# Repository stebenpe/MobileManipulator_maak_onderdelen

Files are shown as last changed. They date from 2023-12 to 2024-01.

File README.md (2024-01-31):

# Maak onderdelen
Om de robot arm op de AMR te plaatsen is een tussen frame nodig. Hier zal ook meteen alle besturingsonderdelen van de MoMa in worden geplaatst. Het frame bestaat uit 4040 en 2020 aluminium frames met beplating er omheen voor stevigheid en afscherming. In het frame zit de besturingskast van de robot arm, safety PLC, embedded AI computer, router en bedingingspaneel met noodstop. De beplating is watergesneden, gebogen, getapped en verzonken. verder zijn er een aantal onderdelen 3D geprint, dit zijn: trap sensoren, houder embedded AI computer, besturingspaneel houder en de kabel buis houders. Dit is geprint met een FDM printer op de trap sensoren na. Deze zijn met een resin printer gemaakt.

## 1. Benodigde onderdelen
1. 2020 ISB aluminium profiel 450mm lang 2X (met M6 getapped gat aan beide kanten)
2. 4040 ISB aluminium profiel 450mm lang 5X
3. ISB M6 t-sleuf 8 moer 20X
4. ISB M5 t-sleuf 5 moer 10X
5. M5X12 verzonken inbus bout 10X
6. M5X20 verzonken inbus bout 4X
7. M5X40 verzonken inbus bout 6X
8. M6X12 verzonken inbus bout 20X
9. 5mm aluminium plaat (voor watersnijden)
10. 3mm aluminium plaat (voor watersnijden)
11. 2mm aluminium plaat (voor watersnijden)
12. M3 inserts 16X (voor de kabel buis 3D print)
13. M6 schroefdraad 500mm lang 5X
14. M6 dopmoer met veer ring en ring 5X
15. M6 moer met ring 1X
16. M10X35 bout met veer ring 2 ringen en een moer 4X

## 2. SolidWorks
Alle onderdelen zijn gemaakt in SolidWorks. Hierin is ook een totaal assembly gemaakt van de MoMa. Hieronder is een renders daarvan te zien.

moma

## 3. 3D prints
De 3D prints zijn gemaakt door een bambu lab en anycubic printer maar een andere 3D printer zou ook moeten werken. De trap sensoren zijn gemaakt door de anycubic 3D printer. Dit is een resin printer, hier is voor gekozen omdat het een best complex onderdeel is met een clip systeem en overhangs. Een resin printer kan dit beter printen dan een FDM printer. De rest van de onderdelen zijn wel geprint door een FDM printer. Dit omdat dit sneller is en minder moeite kost met schoonmaken.

### 3.1 FDM printer
Op de FDM printer zijn de volgende 3D prints genaakt: (als ergens 2X voor staat moet deze 2 keer worden geprint en bij 4X 4 keer)
1. 2X kabel beugel 1.stl
2. 2X kabel beugel 2.stl
3. 2X kabel beugel groot1.stl
4. 2X kabel beugel groot2.stl
5. 4X kabel beugel 3.stl
6. 4X tussen blok controller en top plate.stl
7. 3D print jetson holder boven.stl
8. 3D print jetson holder onder.stl
9. LD 90 panel 3d print.stl

### 3.2 Resin printer
Op de resin printer zijn de volgende 3D prints genaakt:
1. sensor blok L V1.2.stl
2. sensor blok M V1.2.stl
3. sensor blok R V1.2.stl

## 4. Watersnijden
De volgende onderdelen zijn water gesneden: ( als er 2X in staat moet deze 2 keer worden watergesneden. het aan mm van het materiaal zit ook in de naam)
1. 2X side laser holder 2mm.DXF
2. 2X zei plaat 2mm.DXF
3. 3d camera holder 2mm.DXF
4. achterplaat elektra 2mm.DXF
5. Flat pattern - achter plaat sheet metal 2mm.DXF
6. Flat pattern - voor plaat sheet metal 2mm.DXF
7. top plate ld90 3mm.DXF
8. top top plate ld90 5mm.DXF
9. tussen plaat 2X 3mm.DXF
10. tussen plaat met ronding 2X 3mm.DXF

Dit is gedaan met de OMAX 2652 watersnijder:
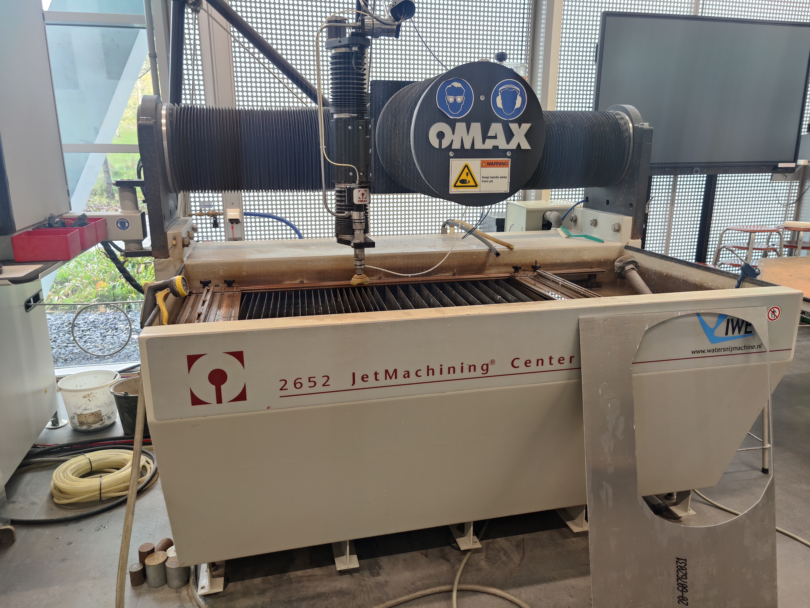
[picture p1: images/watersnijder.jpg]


### 4.1 Buigen
De voor en achter plaat van het frame moeten worden gebogen. Het is handig om eerst een test strip te maken en die te buigen. De voorplaat heeft een lengte nodig van 655,59mm voor de test strip is het handig om deze te af te snijden op een hoogte van 100mm. De achter plaat heeft een lengte van 633,82 en ook hier is het handig om de test strip een hoogte van 100mm te doen. De volgorde van het buigen is eerst de ronding doen en daarna met de kantbank vanaf de buiging naar het einde te werken. De afmetingen en rondingen van de buigen zijn te vinden in de SolidWorks tekening van de betreffende onderdelen. De watergesneden top plate voor de LD-90 is ook goed te gebruiken als referentie bij het buigen. Een voorbeeld van de gebogen test strips is hieronder te zien:



De uiteindelijke platen moeten worden gesneden op een hoogte van 450mm in plaats van de 100mm van de test strips. Ook is het belangrijk om voor het buigen eerst de bramen op de randen weg te halen met vijl en de gaten te verzinken voor een M4 verzonken inbus bout. De test platen kunnen tijdens het buigen ook handig als referentie worden gebruikt.

### 4.2 Verzinken en tappen
De 4 tussenplaten moeten worden getapped met een M4 tap. Verder moeten de voor, achter en zei platen worden verzonken voor een M4 verzonken inbus bout. Let op bij het verzinken dat dit aan de juiste kant wordt gedaan. De voor en achter plaat maakt niet uit maar moet je er vervolgens wel rekening mee houden bij het buigen. Voor de 2 zei platen is het belangrijk dat ze beide aan een andere kant zijn verzonken want deze zijn op die manier gespiegeld. Verder moet er voor de top plate en top top plate verzonken worden voor M6 en M5 verzonken inbus bouten volgens de SolidWorks tekening.

## 5. Trap sensor
Omdat het helaas een keer is gebeurd dat een geleende LD-60 van de trap is gevallen bij NHL-Stenden door de afwezigheid van een trap sensor, hebben we er voor gekozen om een zelfgemaakte trap sensor toe te voegen. Deze zal worden aangesloten op de UserBumper_1-3. Dit werk door een ToF sensor die schuin naar voren kijkt en de data naar een esp32 stuurt. zodra deze een verhoging of verlaging van 30 mm tegen komt zal deze een relais triggeren welke is aangesloten op de UserBumper_1-3 van de LD-90. Hieronder is een programma geschreven in arduino IDE welke te vinden is onder de map trap beveiliging. Hier moet nog een stuk worden toegevoegd voor de WS2812 leds welke in de behuizingen worden geplaatst van de sensoren om de status weer te geven. Hieronder zijn wat renders te zien over hoe het er uit zou moeten zien:

Vooraanzicht 3 trap sensoren             |  Ingezoomd op 1 trap sensor
:-------------------------:|:-------------------------:
  |  

Er is ook een PCB ontworpen voor de trap sensor. De altium bestanden hiervan zijn te vinden in de map trap beveiliging/altium.
Hieronder is een foto te zien van de gemaakte PCB in altium:

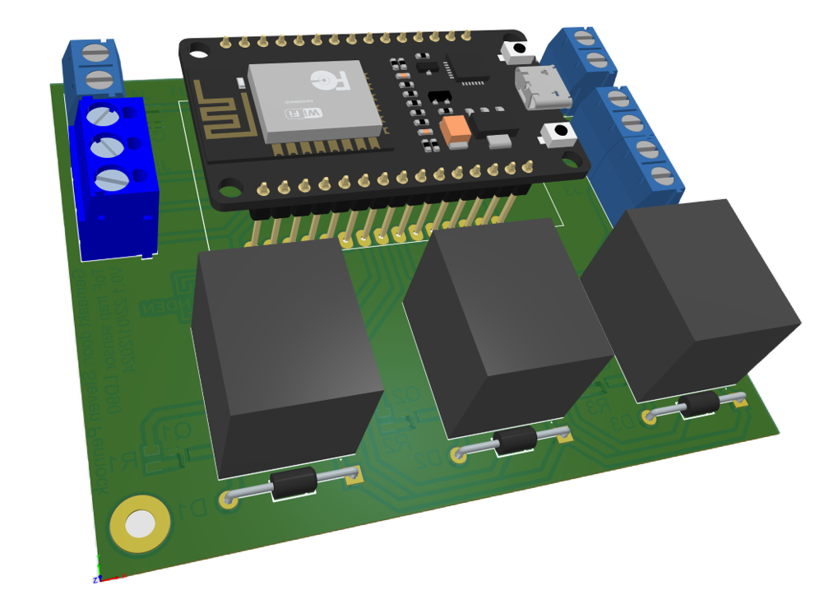
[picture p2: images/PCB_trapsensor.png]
PCB trapsensor


## 6. Monteren en demonteren

### 6.1 Monteren
De montage/demontage van het frame moet met minimaal 2 personen worden gedaan. Dit wegens het gewicht, grote en kostbaarheid.

Bij onduidelijkheden kan je ook kijken naar de SoldWorks assembly, daar is alles te zien zoals de bouten en moeren.

1. Haal de bovenplaat van de LD90 eraf (let op dat er kabels voor de antenne's en HMI aan de LD90 zitten en dat deze niet heel lang zijn).
2. Demonteer de antenne's en de HMI van de bovenplaat. De antenne kabels en de HMI kabel mag bevestigd blijven aan de LD90. De HMI en antenne's moeten wel los worden gehaald van de kabels, deze worden er later weer opgezet.
3. Bevestig de molex connectoren met kabels aan de LD90 IO zoals op onderstaande afbeelding.
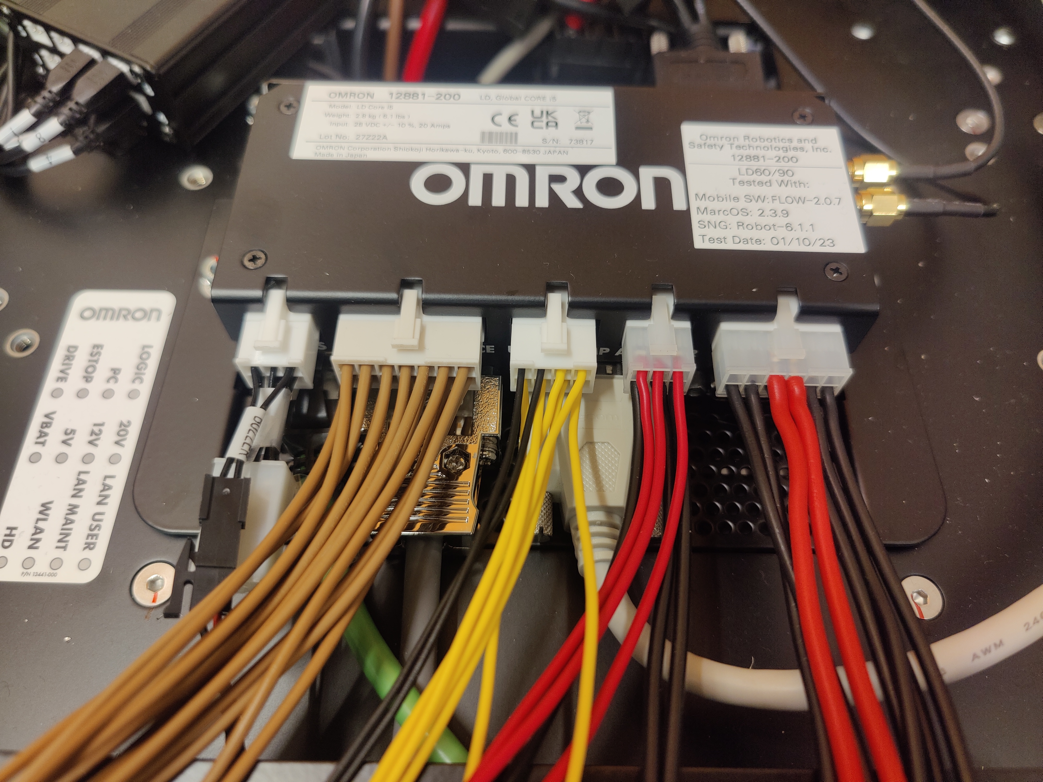
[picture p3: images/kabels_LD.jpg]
kabels


4. Maak de kabels netjes bij elkaar met tie wraps en een spiraalband. Leg alle benodigde kabels bij elkaar aan de voorkant van de LD90, hier zit het gat in de bovenplaat waar de kabels doorheen moeten. Zie onderstaande foto als voorbeeld.
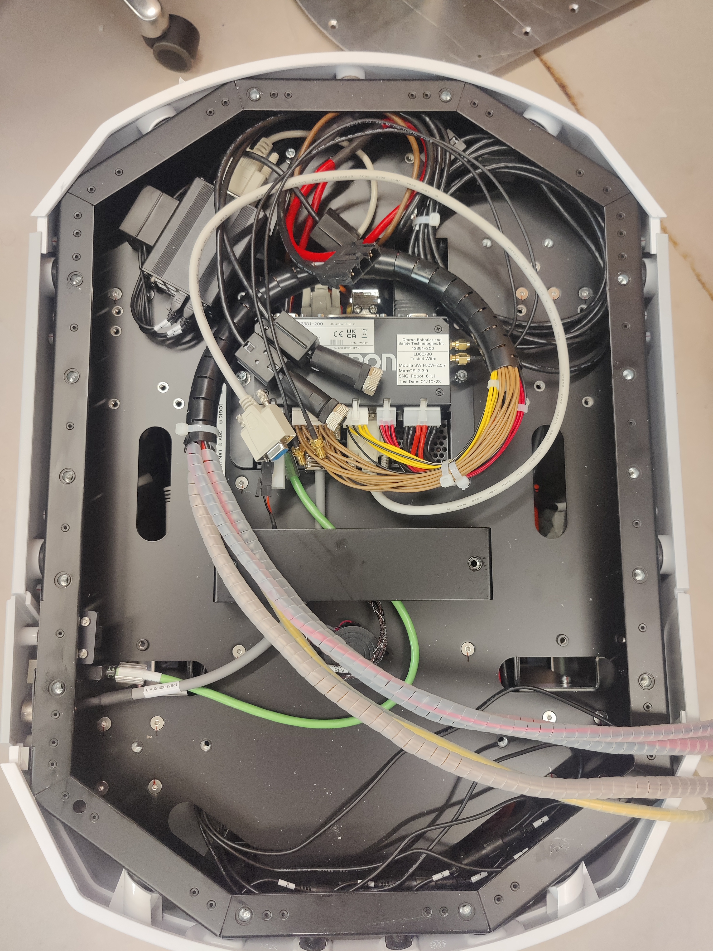
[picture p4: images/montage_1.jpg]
montage_1


5. Vervolgens kan de bovenplaat worden voorbereid voor de montage. Bevestig de robotarm besturingskast en 2020 aluminium frames aan de bovenplaat met M6 verzonken inbus bouten en bevestig 1 van de M6 stafen aan de bovenplaat. De M6 staaf moet wel met een moer en ring aan de onderkant worden bevestigd. Zie onderstaande foto's voor verduidelijking.

Overzicht             |  Moer onder bovenplaat
:-------------------------:|:-------------------------:
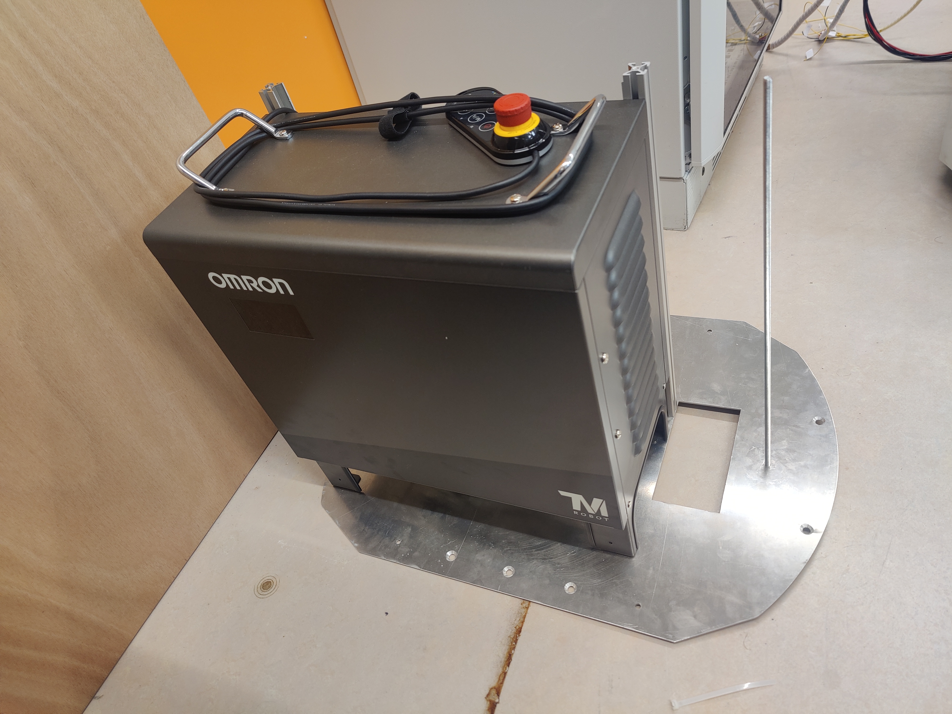
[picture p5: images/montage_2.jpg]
montage_2
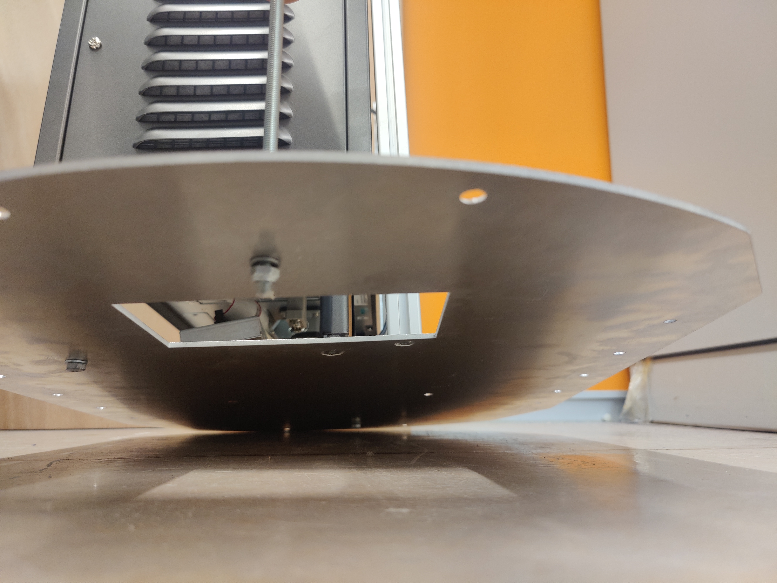
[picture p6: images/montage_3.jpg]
montage_3
  |  

6. Plaats nu de bovenplaat op de LD90. Doe dit met minimaal 2 mensen, 1 iemand die de bovenplaat met besturingskast op de LD90 plaatst en 1 iemand die de kabels door het vierkante gat begeleidt. Dit ziet er dan als volgt uit:
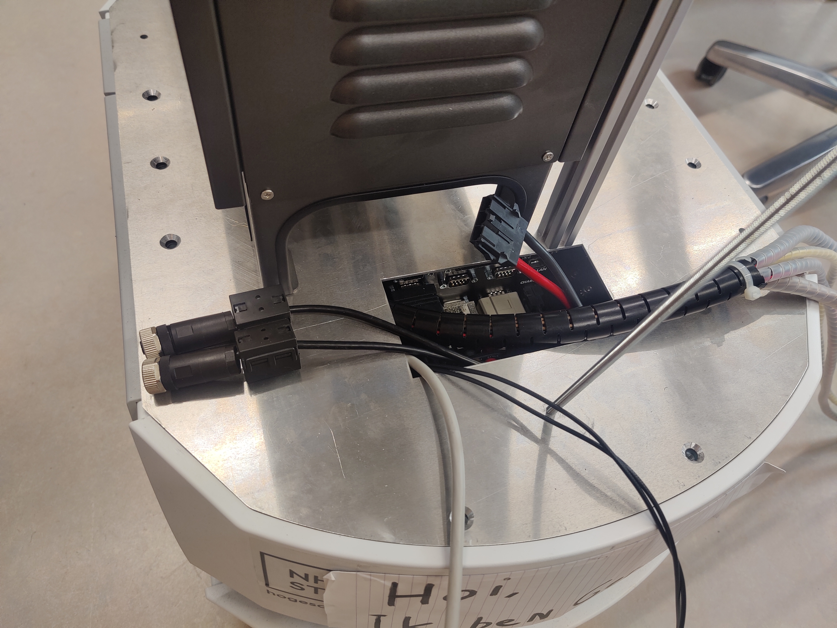
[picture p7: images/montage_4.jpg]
montage_4


7. Bevestig nu een internet kabel aan de user LAN van de LD90. Zie onderstaande foto van de user LAN.
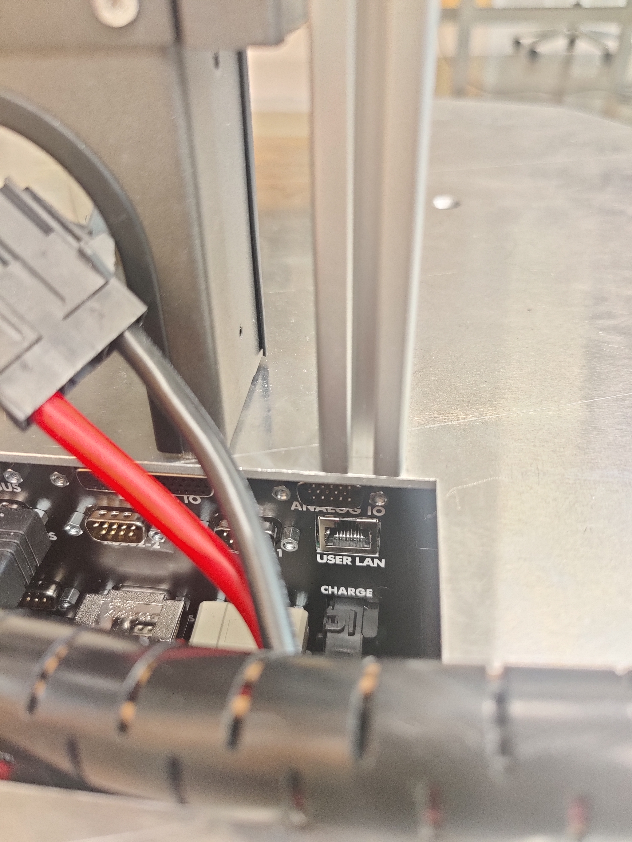
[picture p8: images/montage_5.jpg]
montage_5


8. Plaats de besturingskast op de 2 2020 aluminium profielen en sluit alle kabels aan.

9. Schroef nu de 4 overige M6 stafen aan de bovenplaat. Zie onderstaande foto's voor verduidelijking.
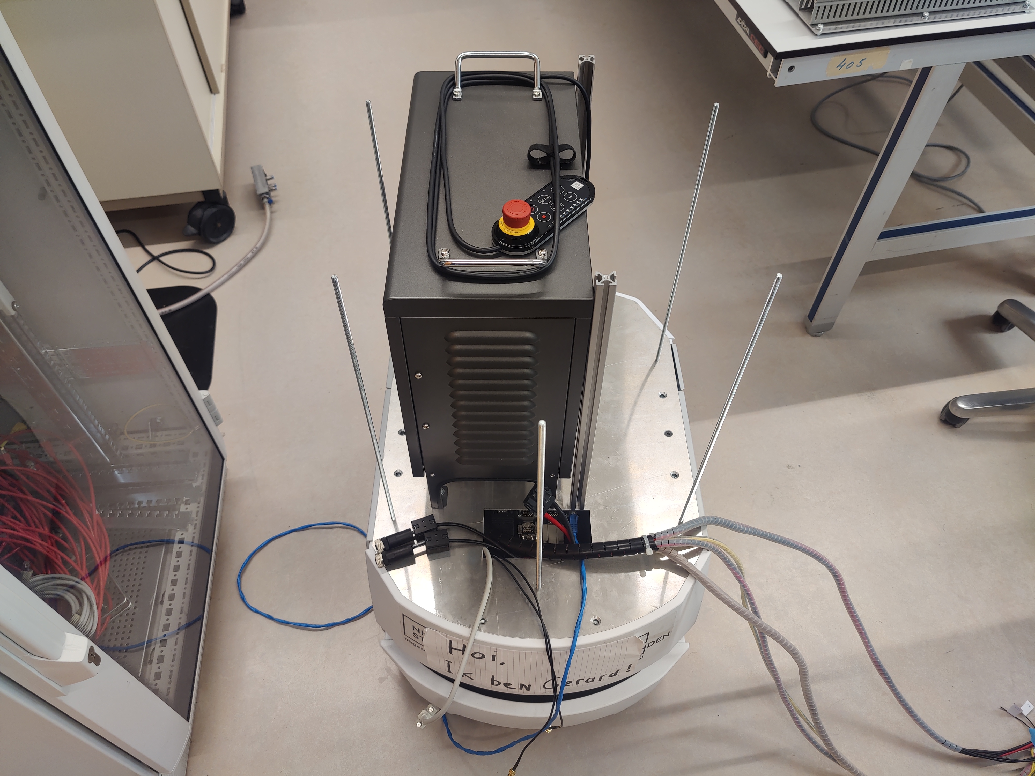
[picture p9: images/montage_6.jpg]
montage_6


10. Bereid de 2 zei platen voor. Hiervoor zijn de volgende onderdelen voor nodig: 4 4040 profielen, 2 zei platen, 2 tussen platen, 2 tussen platen met ronding, 2 side lasers, 2 side laser bevestigingsplaten, 8 M4 verzonken inbus bouten, 6 M6 verzonken inbus bouten en 16 M6 T-sleuf moeren. Zie onderstaande foto van hoe het er uiteindelijk moet uitzien.
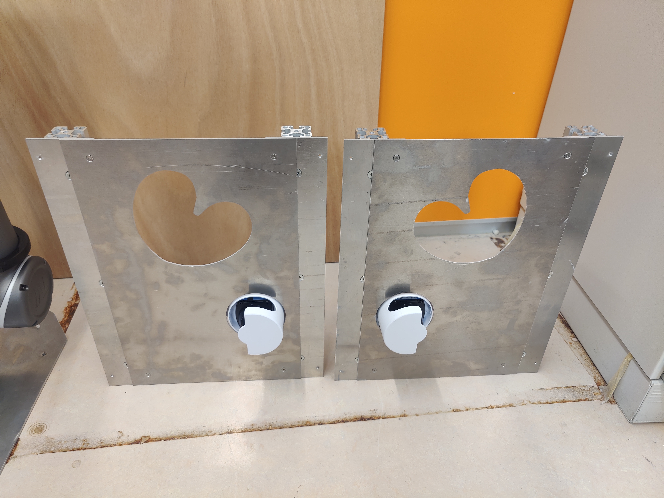
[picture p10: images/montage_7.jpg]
montage_7


11. Plaats de 2 zei platen op de 4 M6 stafen, en plaats de laatste 4040 profiel op de M6 staaf midden voor.

12. Bevestig de HMI en entenne extender kabels op de achterplaat van de LD90. Zie onderstaande foto van de bevestiging van de HMI met de 3D print.

Vooraanzicht             |  Achteraanzicht
:-------------------------:|:-------------------------:
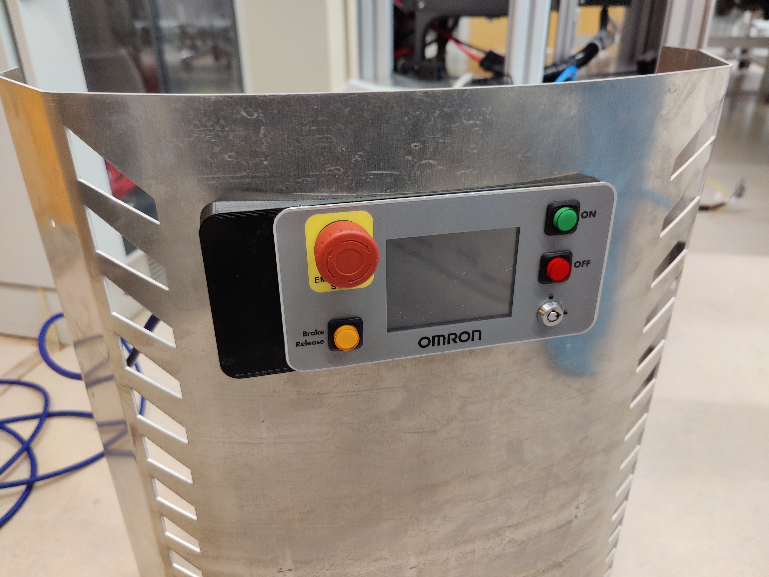
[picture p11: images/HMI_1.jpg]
HMI_1
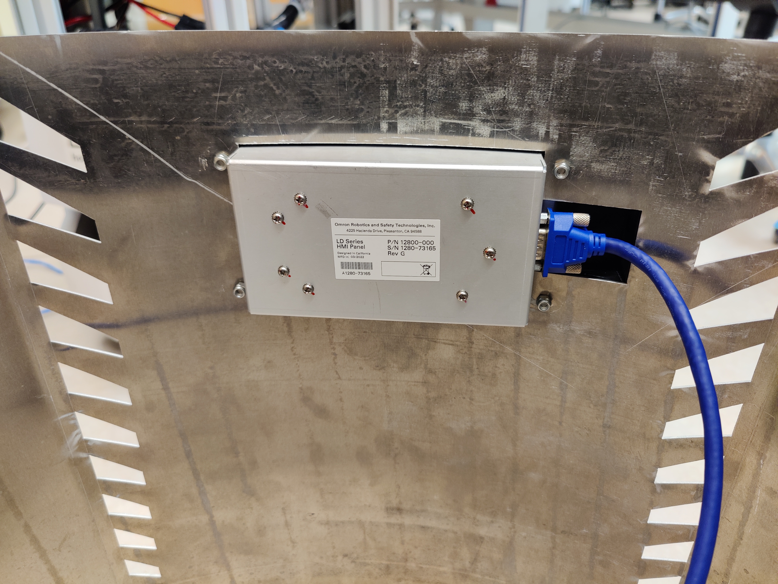
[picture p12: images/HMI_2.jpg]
HMI_2
  |  

## 6.2 Demonteren

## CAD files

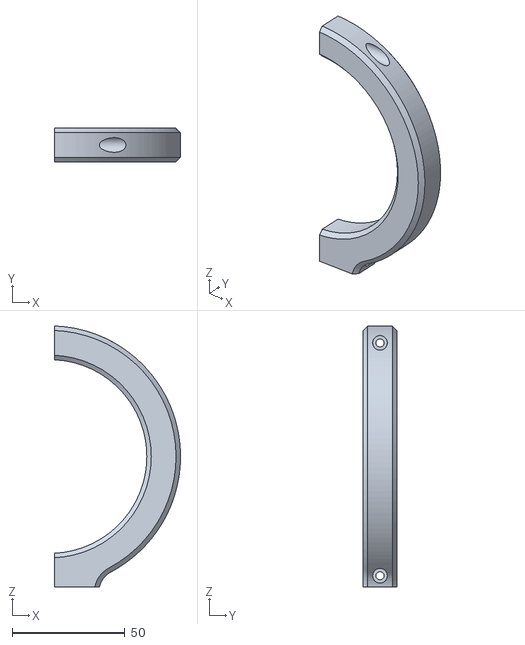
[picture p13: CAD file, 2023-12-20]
3D prints/2X kabel beugel 2.STL
56.0 x 15.0 x 115.9

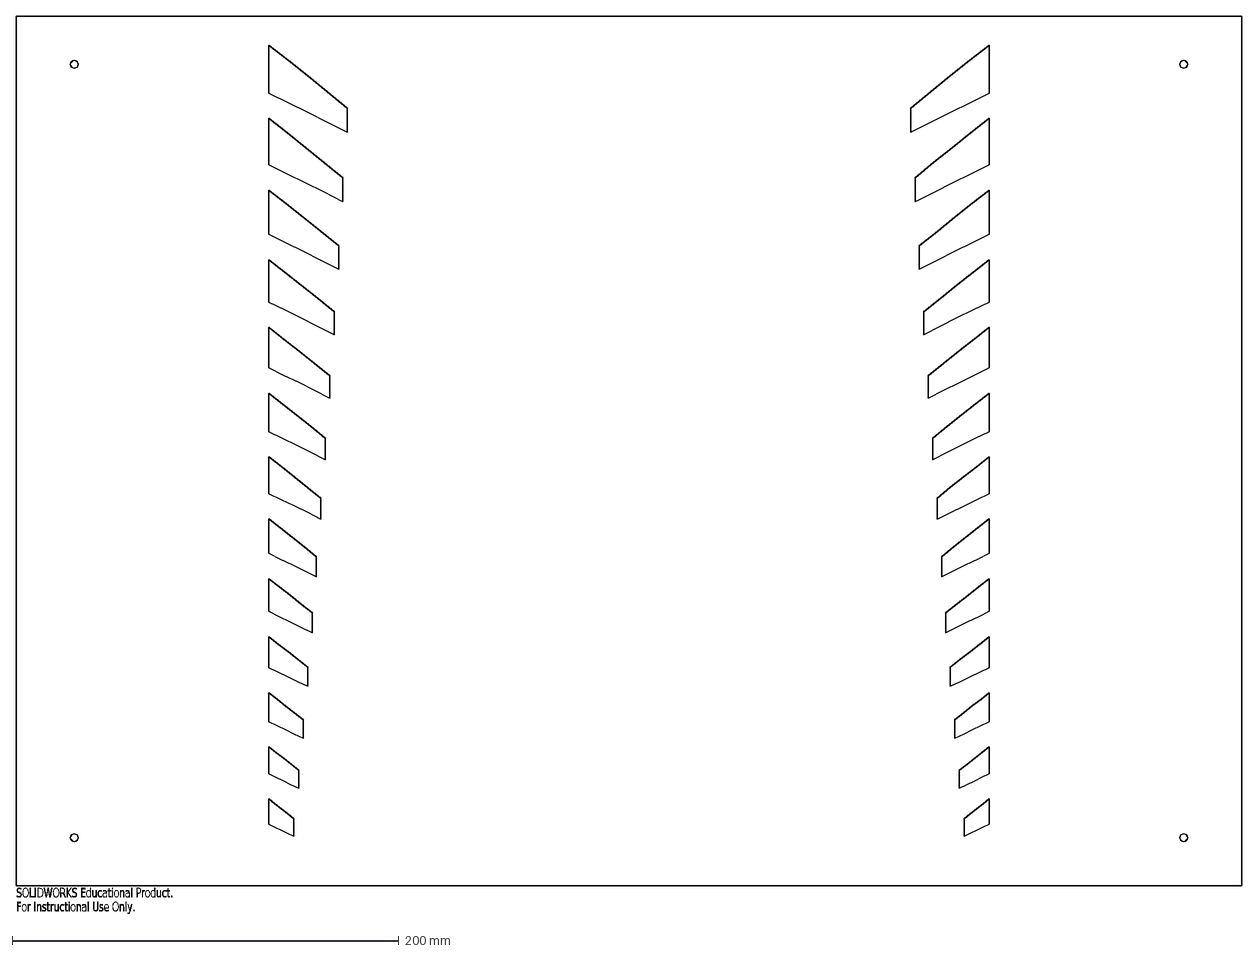
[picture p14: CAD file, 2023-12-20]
watersnijden/Flat pattern - achter plaat sheet metal 2mm.DXF
SOLIDWORKS Educational Product.
For Instructional Use Only.

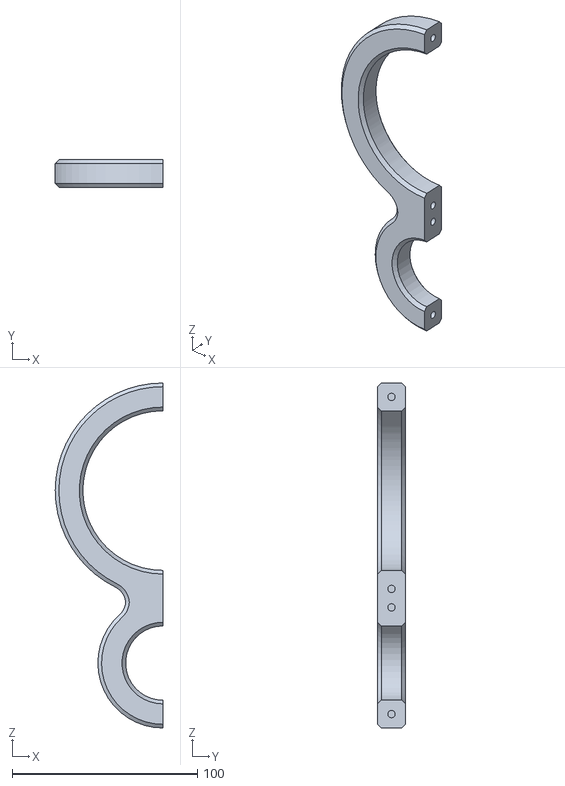
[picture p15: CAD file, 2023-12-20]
3D prints/2X kabel beugel 1.STL
58.0 x 15.0 x 186.0

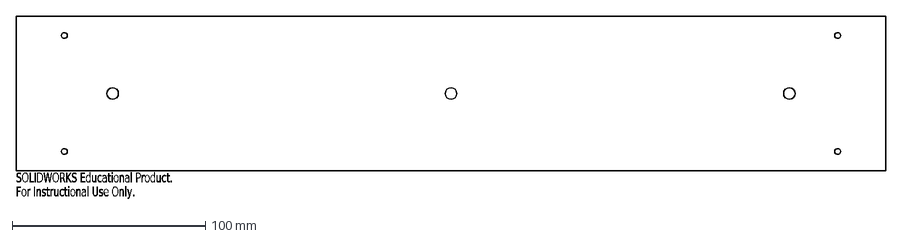
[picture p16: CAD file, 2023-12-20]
watersnijden/tussen plaat 2X 3mm.DXF
SOLIDWORKS Educational Product.
For Instructional Use Only.

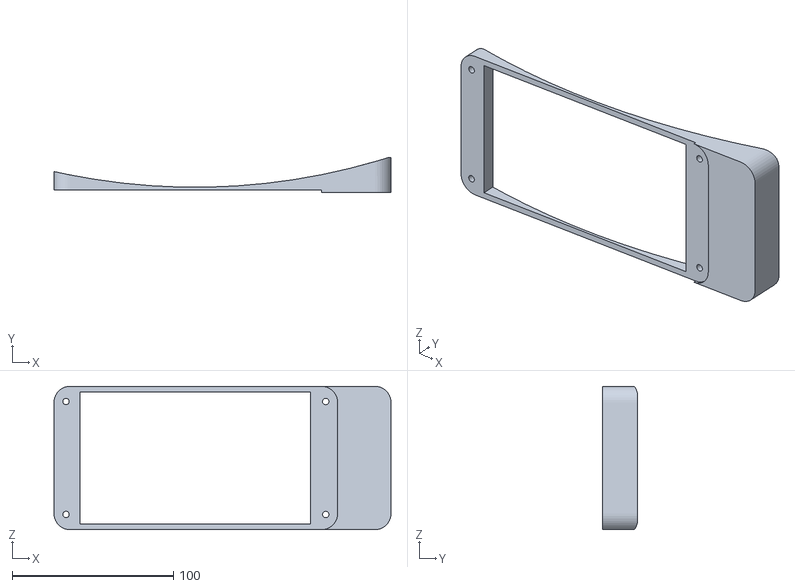
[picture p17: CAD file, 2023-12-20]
3D prints/LD 90 panel 3d print.STL
208.9 x 21.6 x 88.9

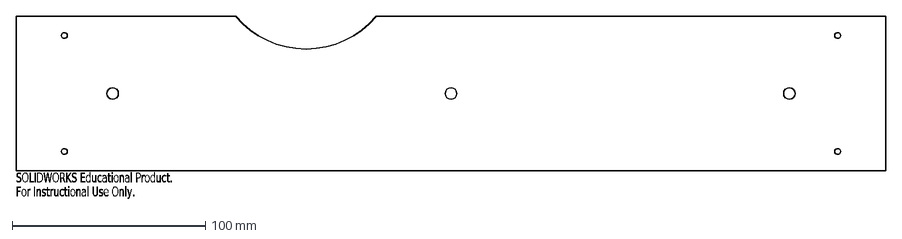
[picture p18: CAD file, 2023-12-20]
watersnijden/tussen plaat met ronding rechts 2X 3mm.DXF
SOLIDWORKS Educational Product.
For Instructional Use Only.

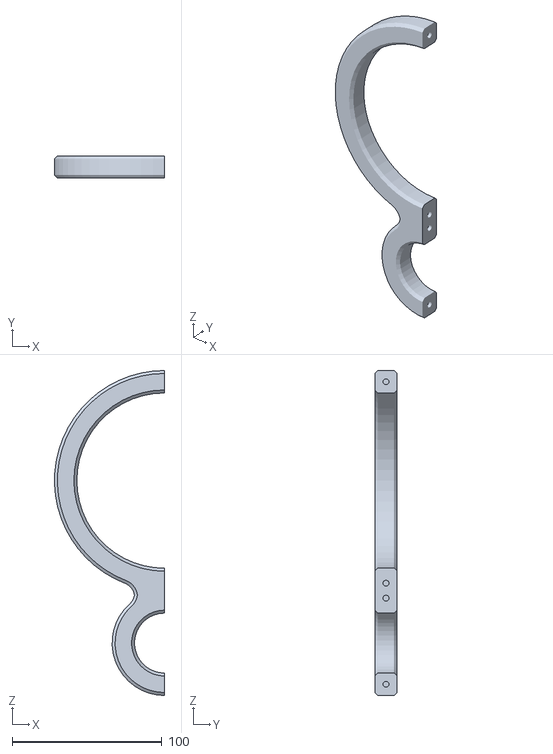
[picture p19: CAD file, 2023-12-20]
3D prints/2X kabel beugel groot1.STL
73.5 x 15.0 x 217.0

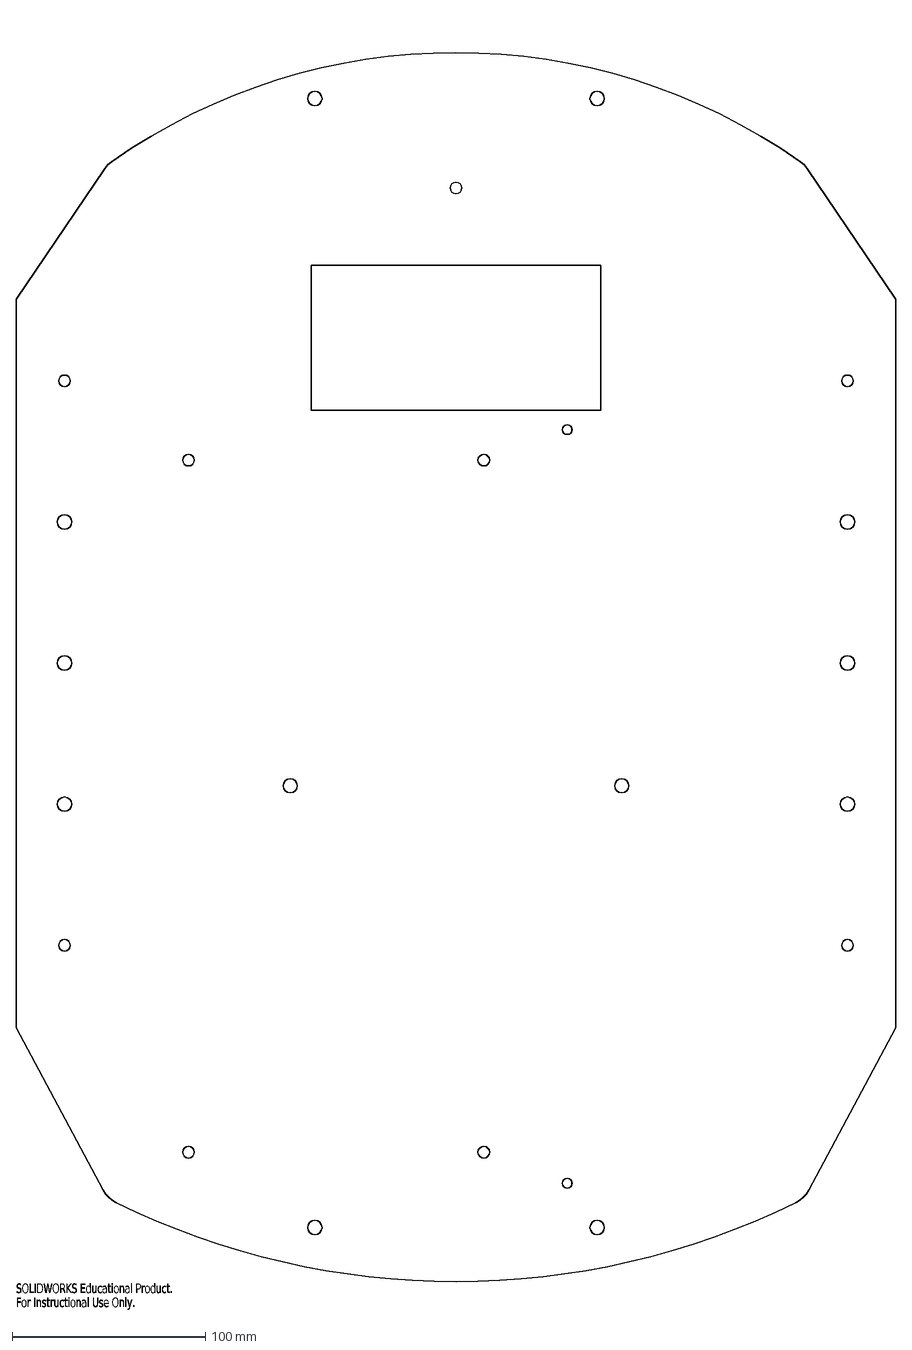
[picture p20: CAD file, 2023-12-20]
watersnijden/top plate ld90 3mm.DXF
SOLIDWORKS Educational Product.
For Instructional Use Only.

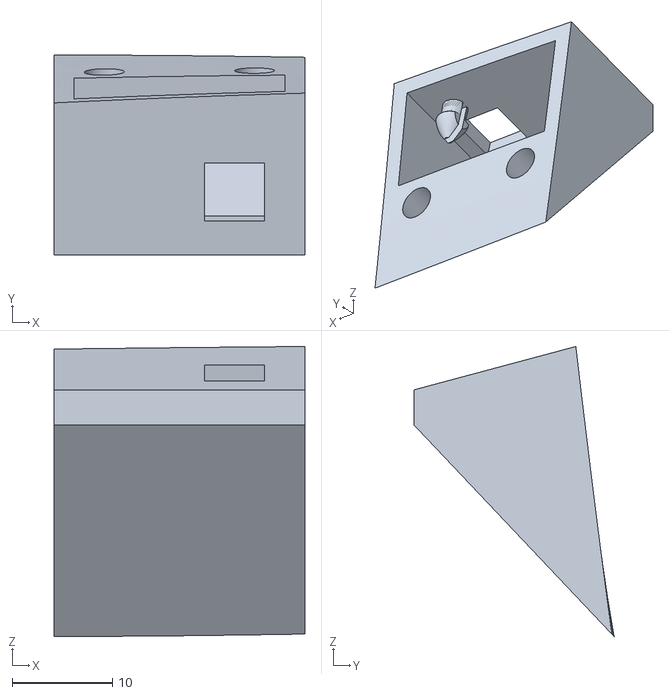
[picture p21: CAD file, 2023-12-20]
3D prints/sensor blok R V1.2.STL
25.0 x 20.0 x 28.9

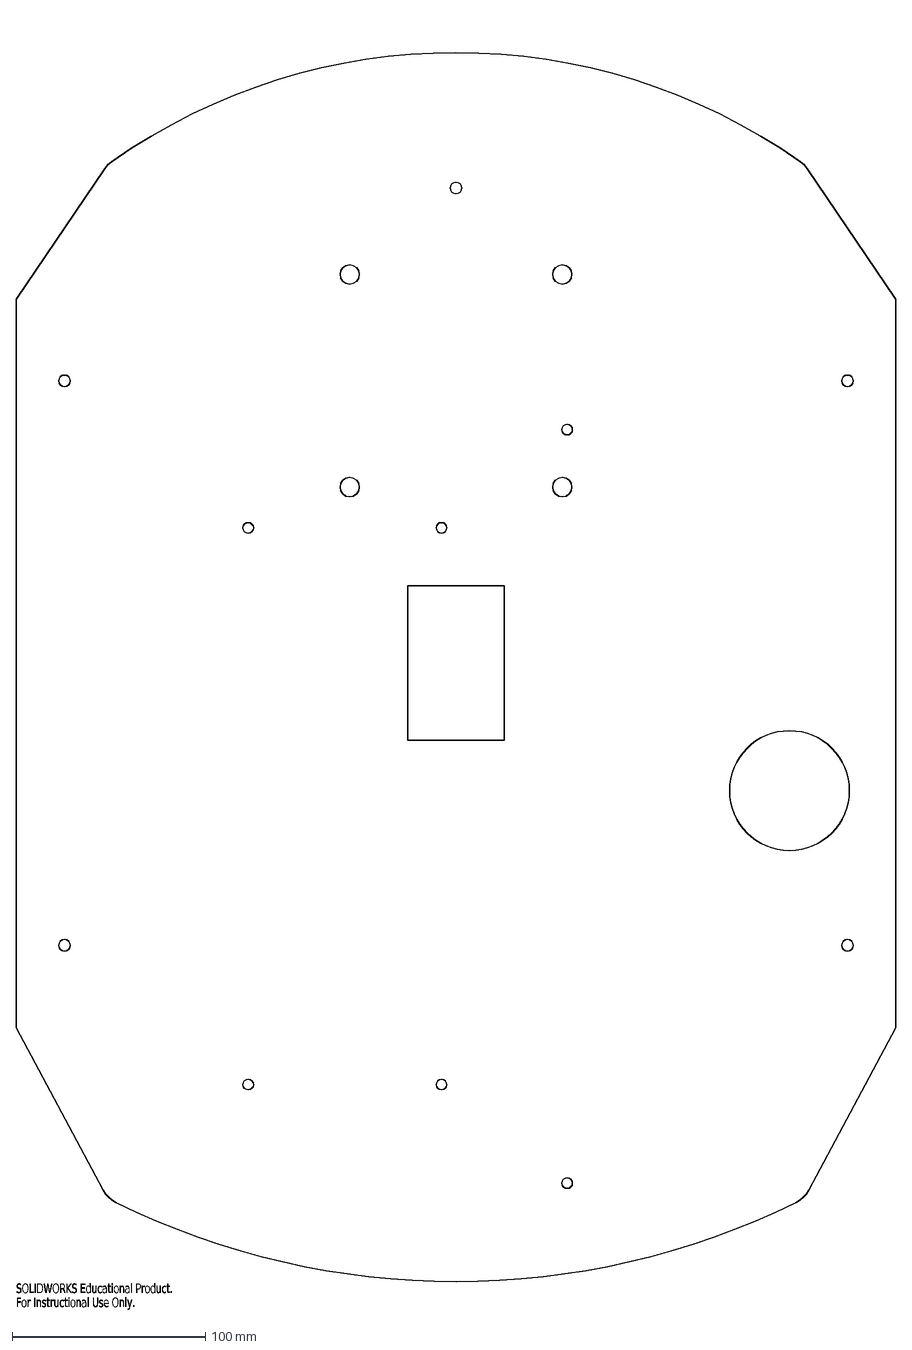
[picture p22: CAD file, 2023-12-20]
watersnijden/top top plate ld90 6mm.DXF
SOLIDWORKS Educational Product.
For Instructional Use Only.

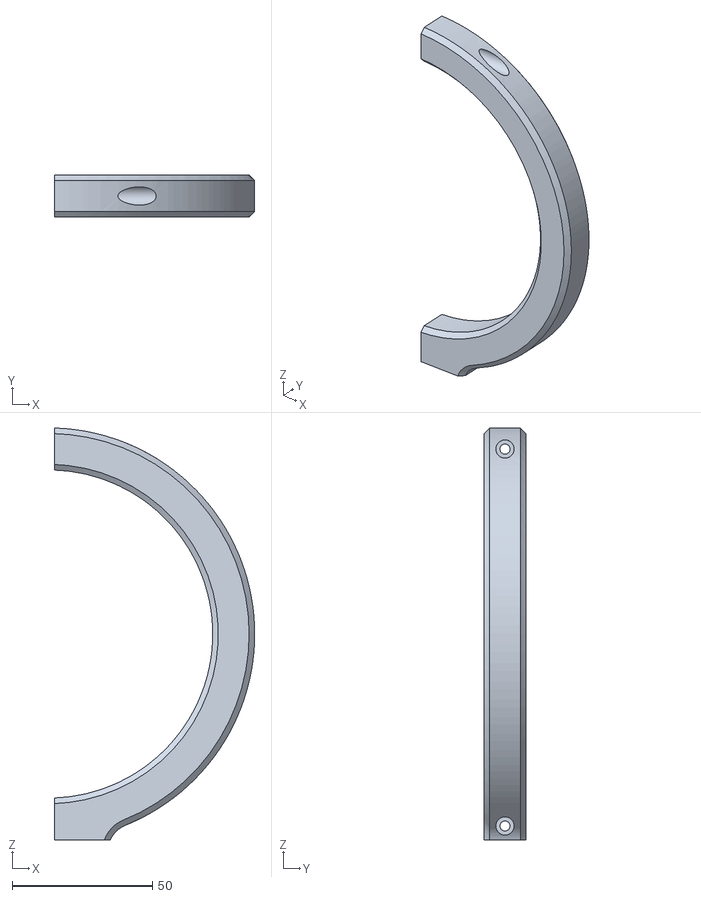
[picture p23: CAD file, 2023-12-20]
3D prints/2X kabel beugel groot2.STL
71.5 x 15.0 x 146.9

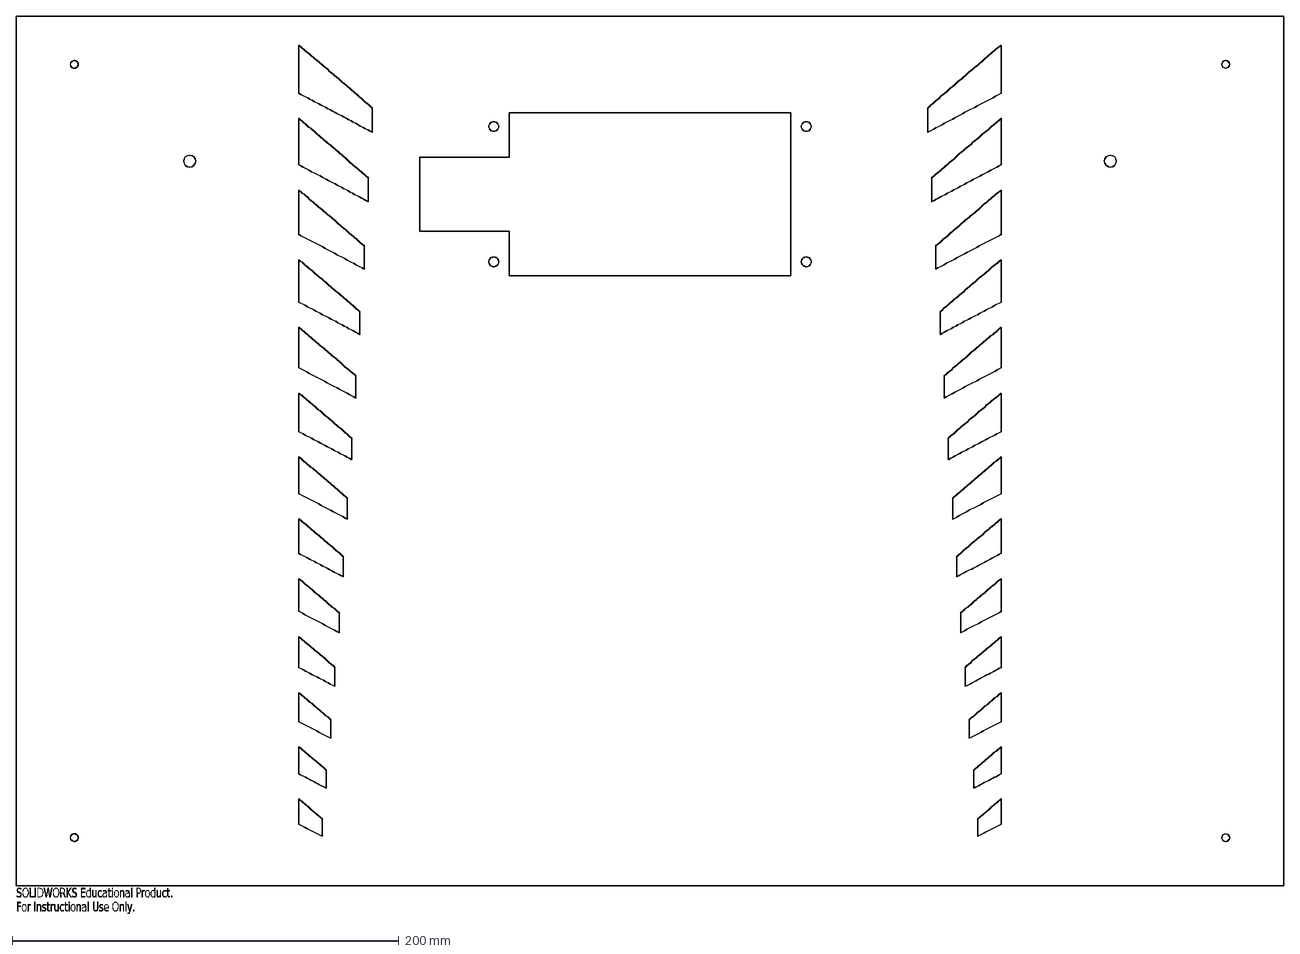
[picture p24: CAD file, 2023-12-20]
watersnijden/Flat pattern - voor plaat sheet metal 2mm.DXF
SOLIDWORKS Educational Product.
For Instructional Use Only.

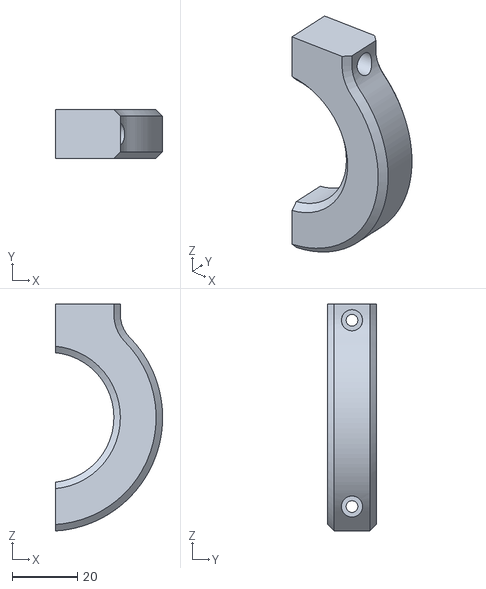
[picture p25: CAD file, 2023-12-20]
3D prints/4X kabel beugel 3.STL
33.0 x 15.0 x 69.8

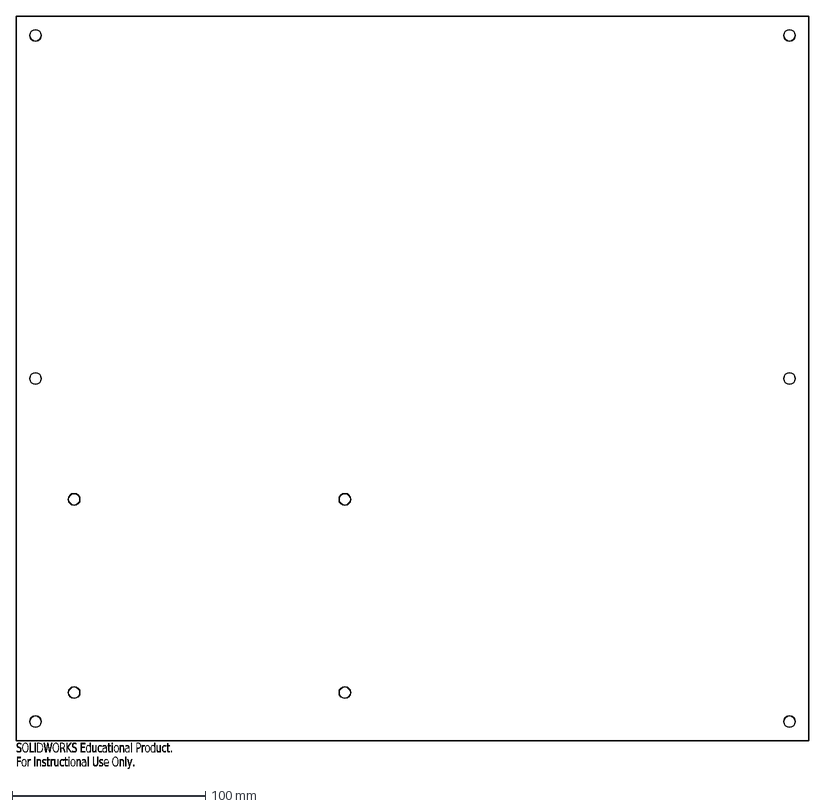
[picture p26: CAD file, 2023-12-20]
watersnijden/achterplaat elektra 2mm.DXF
SOLIDWORKS Educational Product.
For Instructional Use Only.

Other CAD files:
3D prints/sensor blok M V1.2.STL
watersnijden/2X zei plaat 2mm.DXF
3D prints/sensor blok L V1.2.STL
watersnijden/2X side laser holder 2mm.DXF
3D prints/3D-print-jetson-holder-boven.STL
3D prints/3D-print-jetson-holder-onder.STL
3D prints/4X tusssen blok controller en top plate.STL
watersnijden/3d camera holder 2mm.DXF

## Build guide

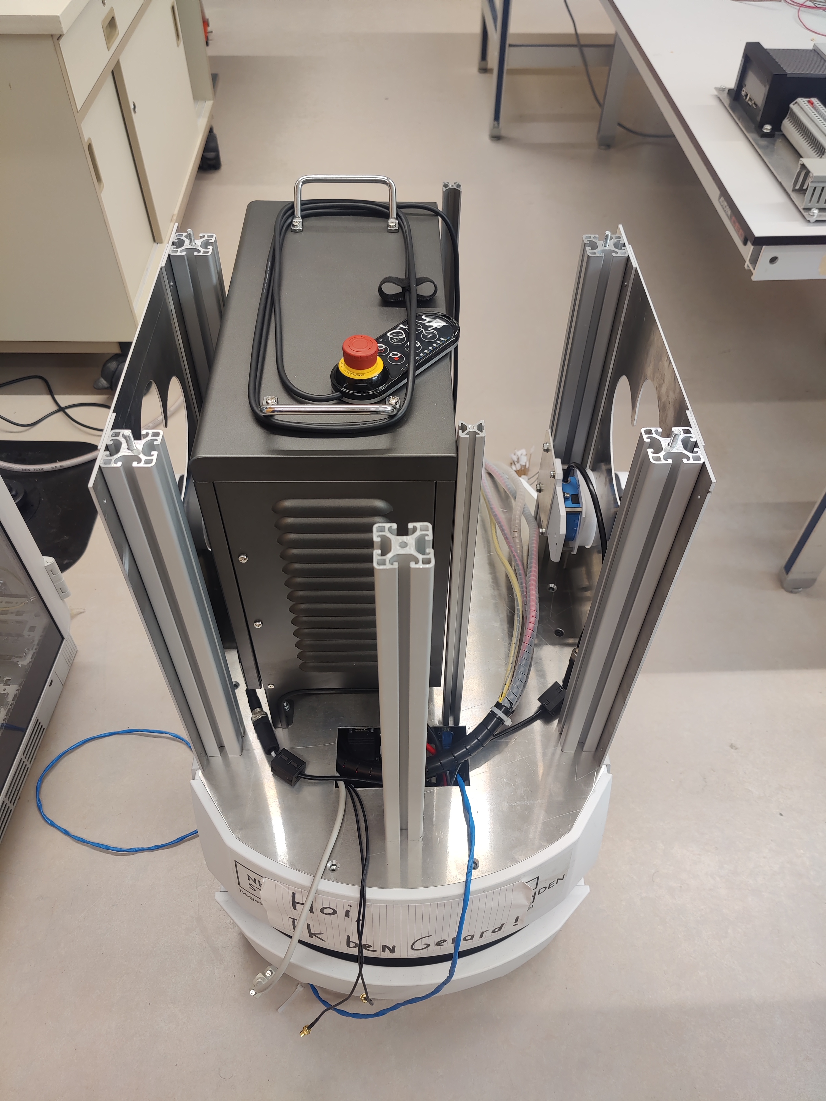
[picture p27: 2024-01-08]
images/montage_11.jpg

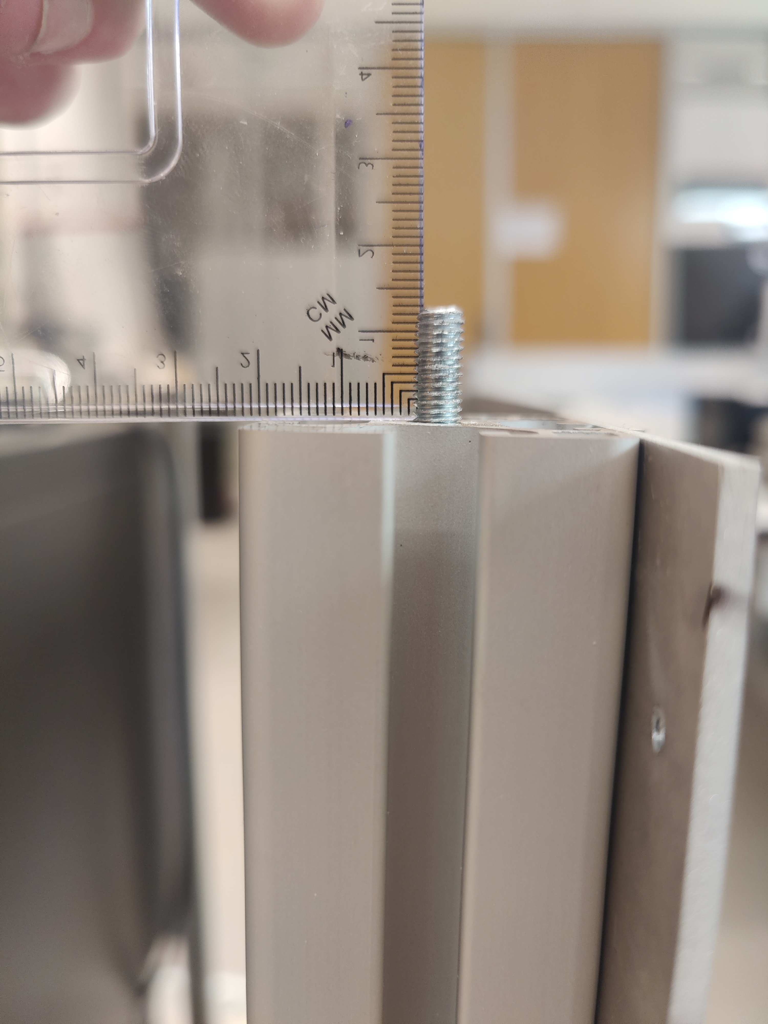
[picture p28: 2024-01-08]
images/montage_10.jpg

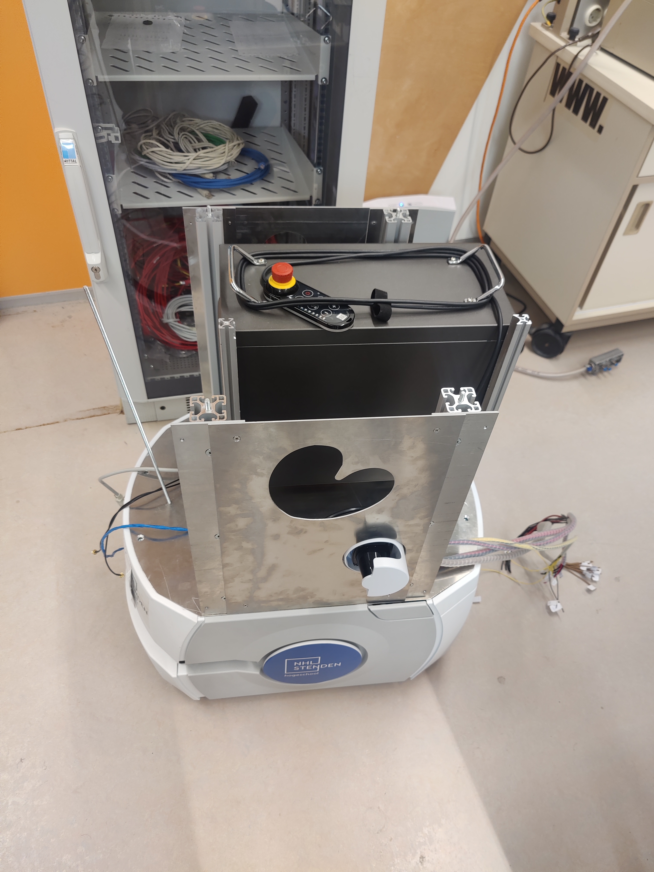
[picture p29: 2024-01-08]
images/montage_8.jpg

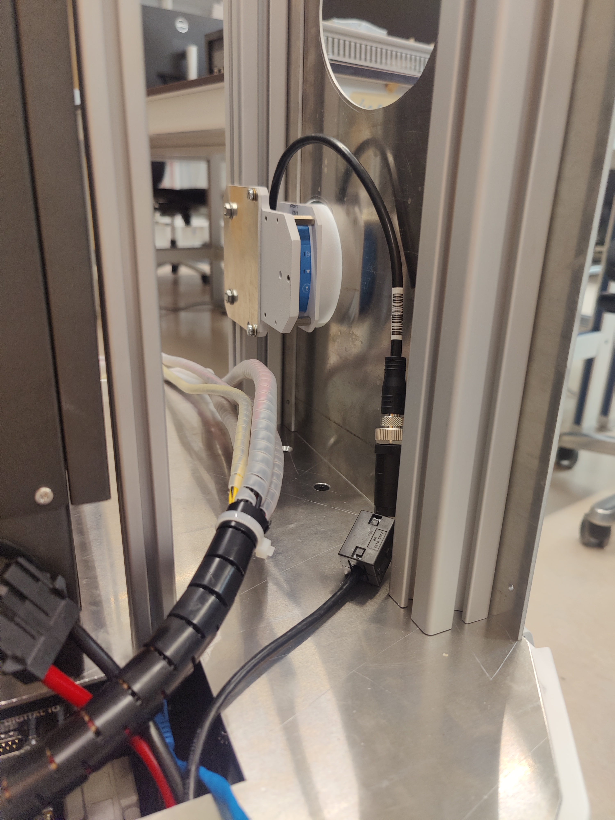
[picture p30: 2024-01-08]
images/montage_9.jpg

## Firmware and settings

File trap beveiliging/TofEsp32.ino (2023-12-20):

#include "Adafruit_VL53L0X.h"

// address we will assign if dual sensor is present
#define LOX1_ADDRESS 0x30
#define LOX2_ADDRESS 0x31
#define LOX3_ADDRESS 0x32

// set the pins to shutdown
#define SHT_LOX1 18
#define SHT_LOX2 19
#define SHT_LOX3 23

// objects for the vl53l0x
Adafruit_VL53L0X lox1 = Adafruit_VL53L0X();
Adafruit_VL53L0X lox2 = Adafruit_VL53L0X();
Adafruit_VL53L0X lox3 = Adafruit_VL53L0X();

// this holds the measurement
VL53L0X_RangingMeasurementData_t measure1;
VL53L0X_RangingMeasurementData_t measure2;
VL53L0X_RangingMeasurementData_t measure3;

void setup(){
  Serial.begin(115200);

  // wait until serial port opens for native USB devices
  while (! Serial){
    delay(1);
  }
  Serial.println(F("serial port opened\n"));
  setID();
  
  // power
  Serial.println(F("VL53L0X API Simple Ranging example\n\n"));
}

void loop(){  
  Serial.print("Reading a measurement... ");

  int distance_total_1 = 0;
  int distance_total_2 = 0;
  int distance_total_3 = 0;
  int max_dis_1 = 0;
  int max_dis_2 = 0;
  int max_dis_3 = 0;
  int min_dis_1 = 1201;
  int min_dis_2 = 1201;
  int min_dis_3 = 1201;
  
  for (int i = 0; i < 6; i++){
    lox1.rangingTest(&measure1, false);
    lox2.rangingTest(&measure2, false);
    lox3.rangingTest(&measure3, false);
    
    if (measure1.RangeStatus != 4){ // phase failures have incorrect data
      distance_total_1 = distance_total_1 + measure1.RangeMilliMeter;
      distance_total_2 = distance_total_2 + measure2.RangeMilliMeter;
      distance_total_3 = distance_total_3 + measure3.RangeMilliMeter;
      
      if(measure1.RangeMilliMeter < min_dis_1){
        min_dis_1 = measure1.RangeMilliMeter;
      }
      if(measure2.RangeMilliMeter < min_dis_2){
        min_dis_2 = measure2.RangeMilliMeter;
      }
      if(measure3.RangeMilliMeter < min_dis_3){
        min_dis_3 = measure3.RangeMilliMeter;
      }
      
      if(measure1.RangeMilliMeter > max_dis_1){
        max_dis_1 = measure1.RangeMilliMeter;
      }
      if(measure2.RangeMilliMeter > max_dis_2){
        max_dis_2 = measure2.RangeMilliMeter;
      }
      if(measure3.RangeMilliMeter > max_dis_3){
        max_dis_3 = measure3.RangeMilliMeter;
      }
    }
    else{
      Serial.println(" out of range ");
    }
  }
  distance_total_1 = distance_total_1 - min_dis_1 - max_dis_1;
  distance_total_2 = distance_total_2 - min_dis_2 - max_dis_2;
  distance_total_3 = distance_total_3 - min_dis_3 - max_dis_3;
  Serial.print("Distance sensor 1 (mm): "); Serial.println(distance_total_1 / 4);
  Serial.print("Distance sensor 2 (mm): "); Serial.println(distance_total_2 / 4);
  Serial.print("Distance sensor 3 (mm): "); Serial.println(distance_total_3 / 4);
}

void setID() {
  // all reset
  digitalWrite(SHT_LOX1, LOW);    
  digitalWrite(SHT_LOX2, LOW);
  digitalWrite(SHT_LOX3, LOW);
  delay(10);
  // all unreset
  Serial.println(F("all low\n"));
  digitalWrite(SHT_LOX1, HIGH);
  digitalWrite(SHT_LOX2, HIGH);
  digitalWrite(SHT_LOX3, HIGH);
  delay(10);
  Serial.println(F("all high\n"));

  // activating LOX1 and resetting LOX2
  digitalWrite(SHT_LOX1, HIGH);
  digitalWrite(SHT_LOX2, LOW);
  digitalWrite(SHT_LOX3, LOW);
  Serial.println(F("setting 1\n"));

  // initing LOX1
  if(!lox1.begin(LOX1_ADDRESS)) {
    Serial.println(F("Failed to boot first VL53L0X"));
    while(1);
  }
  delay(10);
  Serial.println(F("1 set\n"));
  
  // activating LOX2
  digitalWrite(SHT_LOX2, HIGH);
  delay(10);
  Serial.println(F("setting 2\n"));
  //initing LOX2
  if(!lox2.begin(LOX1_ADDRESS)) {
    Serial.println(F("Failed to boot second VL53L0X"));
    while(1);
  }
  delay(10);
  Serial.println(F("2 set\n"));

  // activating LOX3
  digitalWrite(SHT_LOX3, HIGH);
  delay(10);
  Serial.println(F("setting 3\n"));
  //initing LOX3
  if(!lox3.begin(LOX3_ADDRESS)) {
    Serial.println(F("Failed to boot third VL53L0X"));
    while(1);
  }
  Serial.println(F("3 set\n"));
}

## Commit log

2023-12-20 bestanden toegevoegd van MobileManipulator
    [2X kabel beugel 1.STL, 2X kabel beugel 2.STL, 2X kabel beugel groot1.STL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]
2024-01-31 B2 verslag update
    [trap sensor LD PCB.PcbDoc, trap sensor LD schematic.SchDoc, trap_sensor_LD.PrjPcb]
